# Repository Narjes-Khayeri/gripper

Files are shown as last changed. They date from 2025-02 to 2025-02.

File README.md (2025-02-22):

# two finger robotic gripper
# Abstract
This project focused on designing and building a robotic gripper capable of grasping and holding objects up to 70 grams and 5 cm in diameter. A rack and pinion mechanism with a servo motor was used for gripper movement, and a force sensor (FSR) was calibrated to establish the relationship between force and sensor output. A moving average filter was implemented to reduce sensor fluctuations. Object stiffness was measured, and the required grasping force was estimated using linear regression. A P controller was chosen over PID for simplicity and efficiency. Finally, the gripper successfully held various objects, such as paper cups, eggs, and foosball balls, with appropriate force.

# 3D Model 
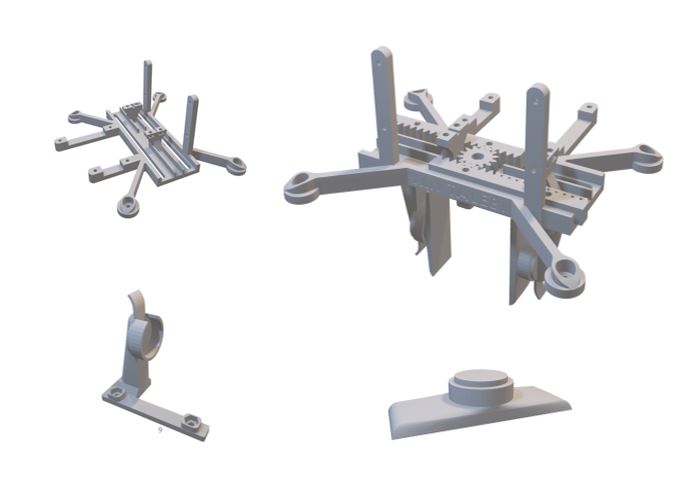
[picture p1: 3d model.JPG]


# FSR Calibration 
In this test, by providing real-world conditions for the sensor and connecting it to the gripper with objects of varying weights, we determined the relationship between the output and the actual value. We also tested this for different series resistances to use the best and most accurate series resistance.
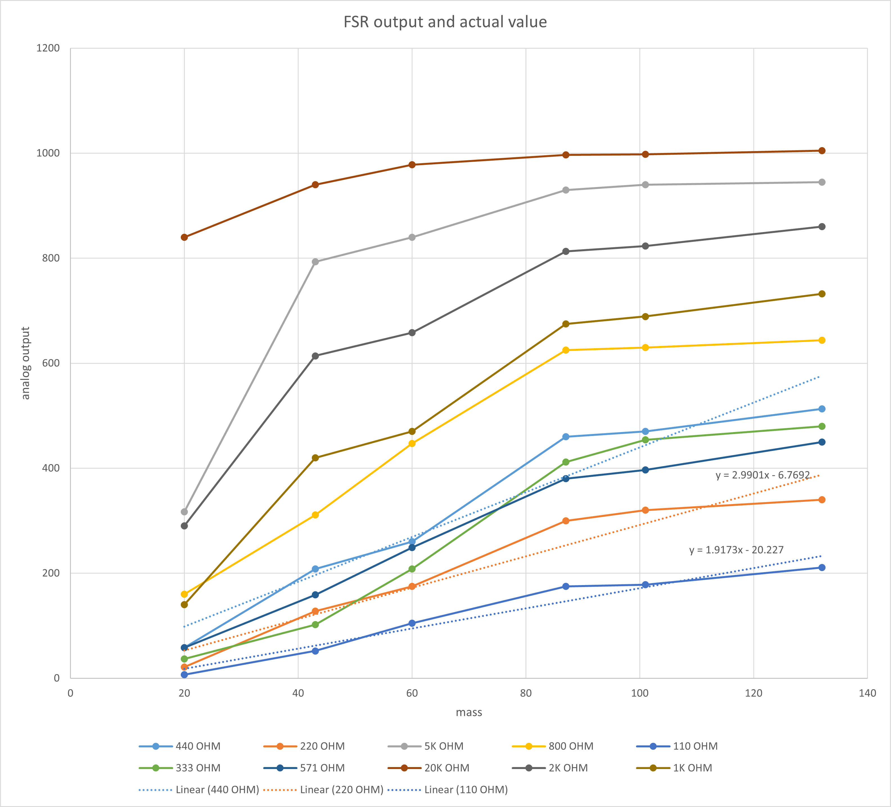
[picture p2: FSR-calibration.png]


 # stiffness detection
 One of the challenges we faced in the project was determining the appropriate force to hold various objects with different masses and stiffnesses. Inspired by an article that assigned specific forces to each stiffness range, we designed a method to obtain the stiffness of objects. By calculating the difference in force and the difference in displacement, the gripper first determines the stiffness coefficient of different objects and then estimates the appropriate force to hold the object.
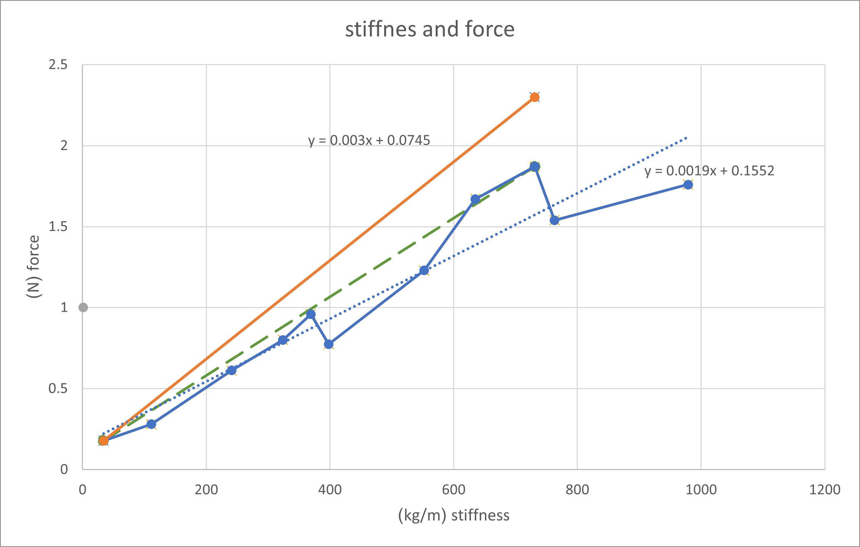
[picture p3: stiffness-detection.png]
 

 # controll method
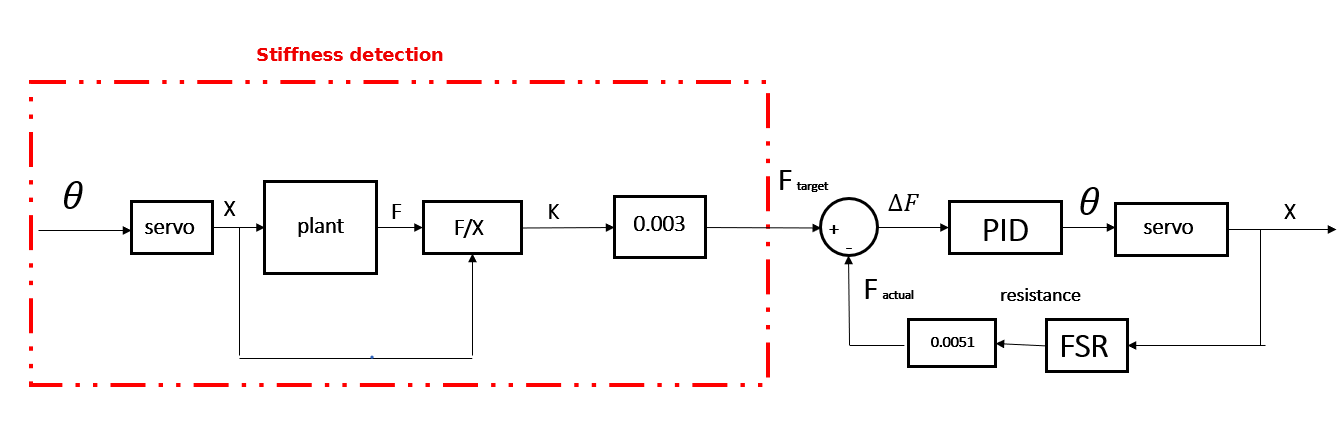
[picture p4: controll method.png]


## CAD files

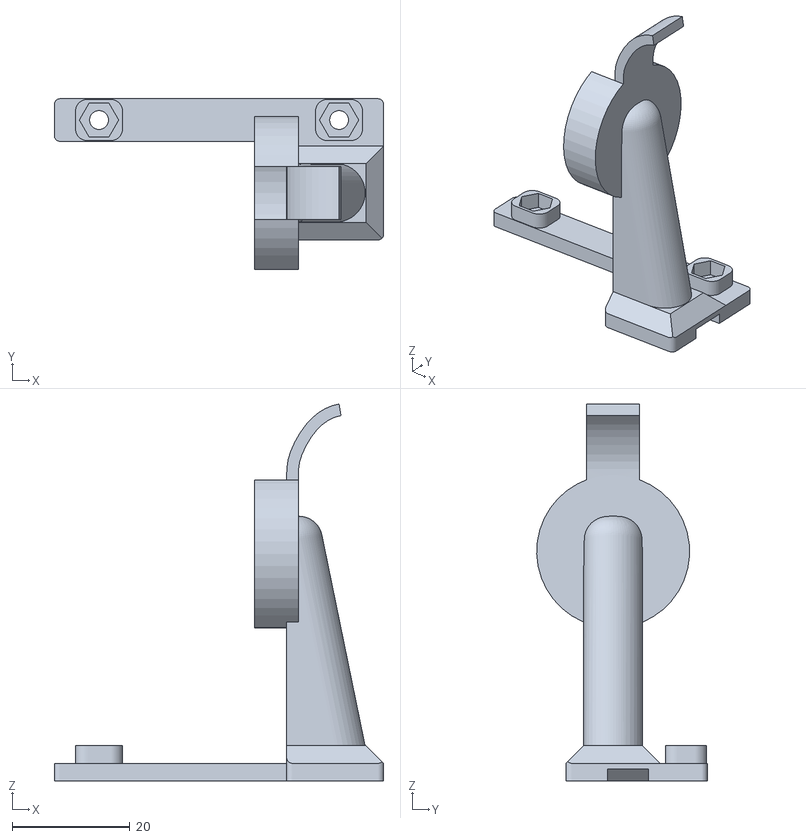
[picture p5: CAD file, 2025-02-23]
3D Model/Jaw_fsr.STL
56.0 x 29.0 x 64.1

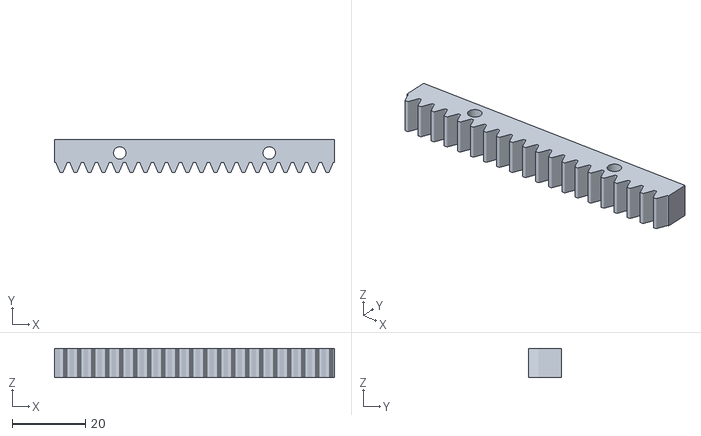
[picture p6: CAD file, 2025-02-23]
3D Model/rack-175-26-14.STL
76.4 x 8.90 x 8.00

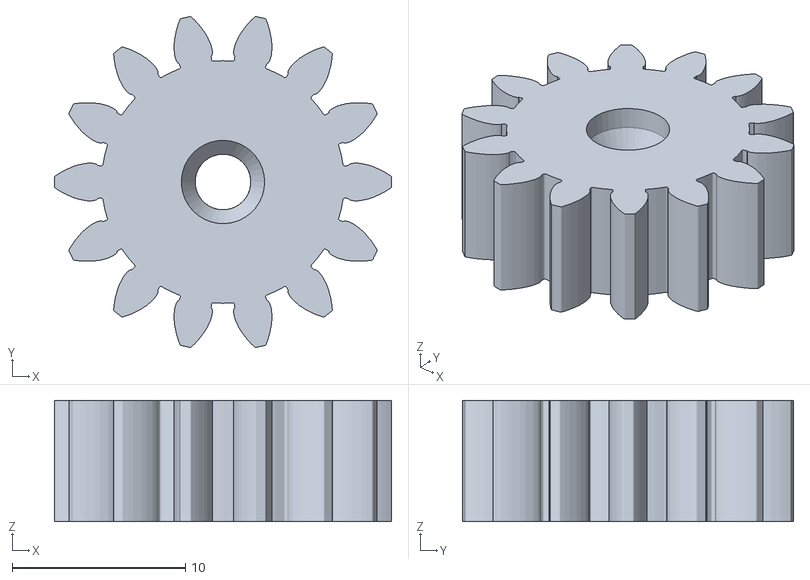
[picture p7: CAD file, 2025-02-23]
3D Model/pinion-175-26-14.STL
19.4 x 19.1 x 7.00

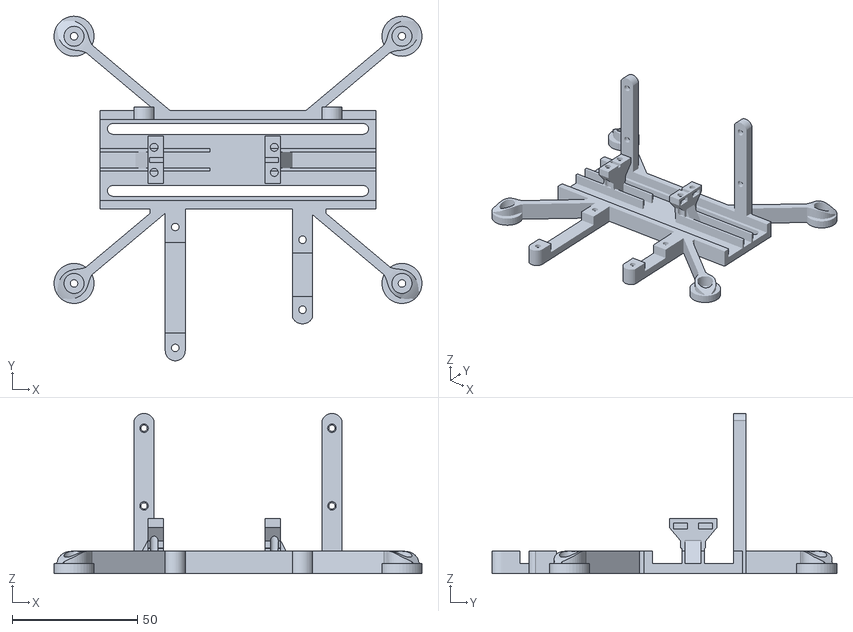
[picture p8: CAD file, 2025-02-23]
3D Model/base.STL
146.9 x 137.5 x 63.9

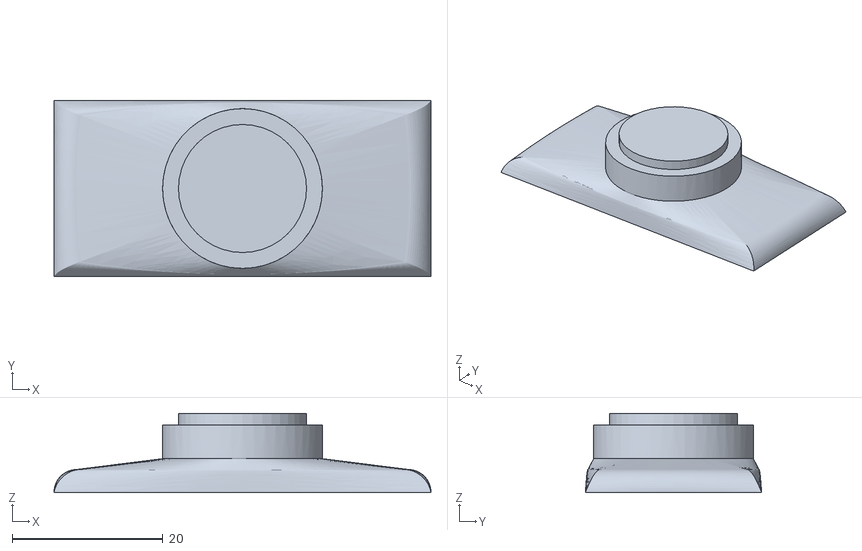
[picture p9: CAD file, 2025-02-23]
3D Model/jaw2.STL
50.0 x 23.4 x 10.5

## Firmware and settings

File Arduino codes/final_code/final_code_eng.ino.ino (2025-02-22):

#include <Servo.h>
#include <LiquidCrystal.h>

// --------------- Pins -----------------
const int buttonPin = 8;  // Button for start
const int servoPin  = 9;  // Servo
const int fsrPin    = A0; // FSR sensor
const int ledPin    = 13; // LED for blinking

// LCD 16x2 in 4-bit mode
// Order: RS, EN, D4, D5, D6, D7
LiquidCrystal lcd(12, 11, 5, 4, 3, 2);

// -------------------- Base Variables --------------------
int   fsrBaseline = 0;       // Baseline after calibration
float fsrFactor   = 0.00511; // Conversion factor from ADC difference to Newton

// Mechanical information
float baseDistance      = 56.0;  // Distance between fingers at 0 degrees
float distancePer175Deg = 52.0;  // Change in distance for 175 degrees

// Servo
Servo myServo;
int servoAngle = 0;

// PID Variables
float Kp = 5.0;
float Ki = 0.0;
float Kd = 0.0;

float integralError = 0.0;
float lastError     = 0.0;
unsigned long lastPIDTime = 0;

// Stiffness and target force
float stiffnessValue   = 0.0;
float initialForce     = 0.0;
float finalForce       = 0.0;
float targetForce      = 0.0;
float lowerBound       = 0.0;
float upperBound       = 0.0;
float finalHoldingForce= 0.0; // Final force that remains within the bounds after PID

// State machine
int state = 0;

/*
   state 0: Waiting for button press
   state 1: Long calibration
   state 2: Stiffness test (holding object until 0.1N + 4 degrees) => only show angle and force while closing
   state 3: Running PID until reaching target force (or timeout) => display "PID in progress..." on LCD
   state 4: Hold for 10 seconds (blink in last 3 seconds) => display stiffness, target force, and final force
   state 5: Open gripper
   state 6: Wait 5 seconds + quick calibration in first 2 seconds + blink in last 3 seconds + return to state=2
*/

// -------------------- Helper Functions --------------------

// Calculate distance between fingers based on servo angle
float getGripperDistance(int angle){
  if(angle > 175) angle = 175;
  return baseDistance - (distancePer175Deg/175.0) * angle;
}

// Read stable FSR (50 samples + remove 4 minimum and 4 maximum)
float getStableForce() {
  const int numSamples = 50;
  int readings[numSamples];

  for(int i=0; i<numSamples; i++){
    readings[i] = analogRead(fsrPin);
    delay(5);
  }

  // Simple sorting
  for(int i=0; i<numSamples-1; i++){
    for(int j=0; j<numSamples-1-i; j++){
      if(readings[j] > readings[j+1]){
        int temp = readings[j];
        readings[j] = readings[j+1];
        readings[j+1] = temp;
      }
    }
  }

  // Remove 4 minimum and 4 maximum values
  long sum = 0;
  int count = 0;
  for(int i=4; i<numSamples-4; i++){
    sum += readings[i];
    count++;
  }

  float avg = sum / (float)count;
  float rawValue = avg - fsrBaseline;
  if(rawValue < 0) rawValue = 0;

  float force = rawValue * fsrFactor;
  return force;
}

// Long calibration
void calibrateFSR() {
  lcd.clear();
  lcd.setCursor(0,0);
  lcd.print("Calibrating...");
  
  const int numReads = 200;
  long sum = 0;
  for(int i = 0; i < numReads; i++){
    sum += analogRead(fsrPin);
    delay(30);
  }
  fsrBaseline = sum / numReads;

  lcd.setCursor(0,1);
  lcd.print("Done Base=");
  lcd.print(fsrBaseline);
  delay(1000);
}

// Quick calibration
void calibrateFSRQuick() {
  lcd.clear();
  lcd.setCursor(0,0);
  lcd.print("Quick Cal...");
  
  const int numReads = 50;
  long sum = 0;
  for(int i=0; i<numReads; i++){
    sum += analogRead(fsrPin);
    delay(20);
  }
  fsrBaseline = sum / numReads;

  lcd.setCursor(0,1);
  lcd.print("Done Base=");
  lcd.print(fsrBaseline);
  delay(800);
}

// Blink LED (3 times, each time 0.5s on + 0.5s off)
void blinkLed3Times(){
  for(int i=0; i<3; i++){
    digitalWrite(ledPin, HIGH);
    delay(500);
    digitalWrite(ledPin, LOW);
    delay(500);
  }
}

// Simple display of "servo angle" and "force" on LCD (two lines)
void displayAngleForce(int angle, float force){
  lcd.clear();
  lcd.setCursor(0,0);
  lcd.print("Angle=");
  if(angle<100) lcd.print("0");
  if(angle<10)  lcd.print("0");
  lcd.print(angle);

  lcd.setCursor(0,1);
  lcd.print("Force=");
  lcd.print(force,2);
}

// Display stiffness, target force, and final force (three parameters)
void displayStiffnessTargetFinal(float stiff, float target, float finalF){
  lcd.clear();
  // Due to limited LCD space, we write it briefly
  // First line: St=? T=?
  lcd.setCursor(0,0);
  lcd.print("St=");
  lcd.print(stiff,2);
  lcd.print(" T=");
  lcd.print(target,2);

  // Second line: F=?
  lcd.setCursor(0,1);
  lcd.print("F=");
  lcd.print(finalF,2);
}

// ----------------------------------------------------------------------
// SETUP
// ----------------------------------------------------------------------
void setup(){
  pinMode(buttonPin, INPUT_PULLUP);
  pinMode(ledPin, OUTPUT);
  digitalWrite(ledPin, LOW);

  lcd.begin(16,2); // LCD 16x2

  myServo.attach(servoPin);
  myServo.write(0);

  // First, enter state 0: Waiting for button press
  state = 0;
}

// ----------------------------------------------------------------------
// LOOP
// ----------------------------------------------------------------------
void loop(){

  switch(state){

    // ------------------------------
    // state 0: Waiting for button press
    // ------------------------------
    case 0:
    {
      // Message on LCD
      lcd.clear();
      lcd.setCursor(0,0);
      lcd.print("Press Button");
      lcd.setCursor(0,1);
      lcd.print("To Start...");

      // Stay here until button is released (HIGH)
      while(digitalRead(buttonPin) == HIGH){
        // Do nothing
      }
      delay(200); // Debounce effect removal
      // When button is pressed:
      state = 1;
    }
    break;

    // ------------------------------
    // state 1: Calibration
    // ------------------------------
    case 1:
    {
      calibrateFSR();
      servoAngle = 0;
      myServo.write(servoAngle);

      // Move to stiffness test
      state = 2;
    }
    break;

    // ------------------------------
    // state 2: Stiffness test (close to 0.1N)
    // ------------------------------
    case 2:
    {
      lcd.clear();
      lcd.setCursor(0,0);
      lcd.print("Meas. Stiffness");

      // 1) Close from angle 0 to 180 until force reaches 0.1N
      for(servoAngle=0; servoAngle<=180; servoAngle++){
        myServo.write(servoAngle);
        float force = getStableForce();

        // As requested: only show angle and force
        displayAngleForce(servoAngle, force);

        if(force >= 0.1){
          initialForce = force;
          break;
        }
      }

      // +4 degrees
      servoAngle += 4;
      if(servoAngle>180) servoAngle=180;
      myServo.write(servoAngle);

      float f2 = getStableForce();
      displayAngleForce(servoAngle, f2);
      finalForce = f2;

      float deltaF = finalForce - initialForce;
      float displacement = 0.001188; // Displacement for 4 degrees
      stiffnessValue = deltaF / displacement;

      delay(800); // Small pause

      state = 3;
    }
    break;

    // ------------------------------
    // state 3: Running PID
    // ------------------------------
    case 3:
    {
      // Simple page for awareness
      lcd.clear();
      lcd.setCursor(0,0);
      lcd.print("PID in progress");

      // Target force = stiffness × 0.0024
      targetForce = stiffnessValue * 0.0024;
      lowerBound  = 0.9 * targetForce;
      upperBound  = 1.1 * targetForce;

      // Prepare PID
      integralError = 0.0;
      lastError = 0.0;
      lastPIDTime = millis();

      // Maximum allowed time
      const unsigned long maxPidTime = 4000; // e.g., 4 seconds
      unsigned long pidStart = millis();

      bool inRange = false;
      finalHoldingForce = 0.0; // Initial zero

      while(true){
        unsigned long now = millis();
        if(now - pidStart > maxPidTime){
          // Time is up
          break;
        }

        float dt = (now - lastPIDTime)/1000.0;
        lastPIDTime = now;

        float force = getStableForce();
        float error = targetForce - force; 

        // PID
        integralError += error * dt;
        float deriv = (error - lastError)/dt;
        lastError = error;

        float output = Kp*error + Ki*integralError + Kd*deriv;

        servoAngle += (int)output;
        if(servoAngle < 0) servoAngle=0;
        if(servoAngle > 180) servoAngle=180;
        myServo.write(servoAngle);

        // If force enters the range, exit
        if(force >= lowerBound && force <= upperBound){
          inRange = true;
          finalHoldingForce = force; // Force when it first entered range
          break;
        }
      }

      if(!inRange){
        // If it failed to enter the range
        finalHoldingForce = getStableForce(); // The value at the end
      }

      state = 4; // Move to holding
    }
    break;

    // ------------------------------
    // state 4: Holding for 10 seconds
    // ------------------------------
    case 4:
    {
      // Throughout the 10s, show stiffness, target force, and final force
      // Write at the beginning and do not change until the end of 10s
      displayStiffnessTargetFinal(stiffnessValue, targetForce, finalHoldingForce);

      unsigned long startTime = millis();
      unsigned long holdDuration = 10000; 
      bool blinkedYet = false;

      while(true){
        unsigned long elapsed = millis() - startTime;
        if(elapsed >= holdDuration) break; // End of 10s

        // Blink in last 3 seconds
        if(elapsed >= 7000 && !blinkedYet){
          blinkLed3Times();
          blinkedYet = true;
        }
        delay(50);
      }

      state = 5;
    }
    break;

    // ------------------------------
    // state 5: Open gripper
    // ------------------------------
    case 5:
    {
      lcd.clear();
      lcd.setCursor(0,0);
      lcd.print("Releasing...");
      servoAngle = 0;
      myServo.write(servoAngle);
      delay(500);

      state = 6;
    }
    break;

    // ------------------------------
    // state 6: 5s wait + quick calibration + blink
    // ------------------------------
    case 6:
    {
      lcd.clear();
      lcd.setCursor(0,0);
      lcd.print("Wait 5s...");
      
      unsigned long startTime = millis();
      bool calDone   = false;
      bool blinkDone = false;

      while(true){
        unsigned long elapsed = millis() - startTime;
        if(elapsed >= 5000) break;

        // First 2s: quick calibration
        if(elapsed < 2000 && !calDone){
          calibrateFSRQuick();
          calDone = true;
        }
        // Last 3s: blink
        if(elapsed >= 2000 && !blinkDone){
          blinkLed3Times();
          blinkDone = true;
        }
        delay(50);
      }

      // End of cycle, go back to state=2 for the next object
      state = 2;
    }
    break;
  } // switch
}

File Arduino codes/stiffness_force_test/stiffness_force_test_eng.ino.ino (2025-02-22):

#include <Servo.h>

const int fsrPin = A0;         // FSR sensor pin
int fsrBaseline = 0;           // Baseline value obtained after calibration
const float fsrFactor = 0.00511; // Conversion factor from ADC difference to Newton (based on experiment)

// Function to store and sort ADC data
// and get the average after removing extreme samples
float getStableForce() {
  const int numSamples = 50;   // Number of samples to take
  int readings[numSamples];

  // Sampling
  for(int i = 0; i < numSamples; i++){
    readings[i] = analogRead(fsrPin);
    delay(5); // Interval between each sample (5ms)
  }

  // Sorting readings using a simple method (bubble sort or any preferred method)
  for(int i = 0; i < numSamples - 1; i++){
    for(int j = 0; j < numSamples - i - 1; j++){
      if(readings[j] > readings[j+1]) {
        int temp = readings[j];
        readings[j] = readings[j+1];
        readings[j+1] = temp;
      }
    }
  }

  // Remove 2 minimum and 2 maximum samples
  // (to reduce the impact of noise and outlier data)
  long sum = 0;
  int count = 0;
  for(int i = 4; i < numSamples - 2; i++){
    sum += readings[i];
    count++;
  }

  // Average of middle samples
  float avgReading = sum / (float)count;

  // Subtract baseline value
  float rawValue = avgReading - fsrBaseline;
  if(rawValue < 0) {
    rawValue = 0;
  }

  // Calculate force (in Newton)
  float force = rawValue * fsrFactor;
  return force;
}

Servo myServo;              // Servo object
int servoAngle = 0;         // Servo angle (0 to 180 degrees)

// Variables for stiffness test
bool stiffnessTestDone = false;   
float initialForce = 0.0;   // Initial force when reaching 0.1N
float finalForce = 0.0;     // Force after an additional 4 degrees of movement
float stiffnessValue = 0.0; // Stiffness value
float deltaForce = 0.0;     // Force difference (finalForce - initialForce)

// =========================
// Sensor calibration function
// =========================
void calibrateFSR(int pin) {
  Serial.println("Calibrating the sensor...");

  // Read the sensor multiple times to get an average and use it as baseline
  const int numReads = 200;
  long sum = 0;
  for (int i = 0; i < numReads; i++) {
    sum += analogRead(pin);
    delay(30);
  }
  fsrBaseline = sum / numReads; // Average value read
  Serial.print("Baseline value is: ");
  Serial.println(fsrBaseline);
  Serial.println("Calibration done. Starting main loop...");
  delay(1000);
}

void setup() {
  Serial.begin(9600);   // Begin serial communication
  myServo.attach(9);    // Attach servo to digital pin 9

  // First, calibrate the sensor
  calibrateFSR(fsrPin);

  // Set the gripper to fully open (zero angle)
  servoAngle = 0;
  myServo.write(servoAngle);
}

void loop() {

  // Until stiffness test is completed:
  if (!stiffnessTestDone) {

    // Move from angle 0 to 180; for each step:
    // 1) Close the servo by 1 degree
    // 2) Read the force using getStableForce() (about ~250ms each time)
    // 3) Print the force
    // 4) If force >= 0.1N, stop
    for (servoAngle = 0; servoAngle <= 180; servoAngle++) {
      myServo.write(servoAngle);

      // Read the stable force using the function above
      float force = getStableForce();

      // Report angle and force with decimal precision
      Serial.print("Angle: ");
      Serial.print(servoAngle);
      Serial.print(" degrees, Force: ");
      Serial.print(force, 3); // Three decimal places
      Serial.println(" Newton");

      // Check if the force threshold is reached
      if (force >= 0.1) {
        initialForce = force; // Initial force at the threshold
        break; // Exit the loop
      }
    }

    // Now close the servo by an additional 4 degrees
    servoAngle += 4;
    if (servoAngle > 180) {
      servoAngle = 180; // Prevent going beyond 180 degrees
    }
    myServo.write(servoAngle);

    // Read the force again
    finalForce = getStableForce();

    // Calculate stiffness
    deltaForce = finalForce - initialForce;
    float displacement = 0.001188; // Meters (displacement between the two fingers at 4 degrees)
    stiffnessValue = deltaForce / displacement;

    // Report stiffness and force difference
    Serial.println("==================================");
    Serial.print("Initial Force (N): ");
    Serial.println(initialForce, 3);
    Serial.print("Final Force (N): ");
    Serial.println(finalForce, 3);
    Serial.print("Force Difference (DeltaF) = ");
    Serial.print(deltaForce, 3);
    Serial.println(" N");
    Serial.print("Object Stiffness (N/m) = ");
    Serial.print(stiffnessValue, 3);
    Serial.println(" N/m");
    Serial.println("==================================");

    // Test completion message
    Serial.println("Stiffness test is complete. Waiting for serial commands (+ or -).");

    // Now the test is finished, and we will enter manual control mode
    stiffnessTestDone = true;
  }
  else {
    // In this phase, the test is complete and we are only waiting for serial commands
    // If '+' is received -> close by one degree
    // If '-' is received -> open by one degree
    // Then read and report the force
    if (Serial.available() > 0) {
      char command = Serial.read();

      if (command == '+') {
        servoAngle++;
        if (servoAngle > 180) {
          servoAngle = 180; // Prevent going beyond 180
        }
        myServo.write(servoAngle);

        // Read and display the force
        float force = getStableForce();
        Serial.print("Angle: ");
        Serial.print(servoAngle);
        Serial.print(" degrees, Force: ");
        Serial.print(force, 3);
        Serial.println(" Newton");
      }
      else if (command == '-') {
        servoAngle--;
        if (servoAngle < 0) {
          servoAngle = 0; // Prevent going below 0
        }
        myServo.write(servoAngle);

        // Read and display the force
        float force = getStableForce();
        Serial.print("Angle: ");
        Serial.print(servoAngle);
        Serial.print(" degrees, Force: ");
        Serial.print(force, 3);
        Serial.println(" Newton");
      }
      // If any other command is received, it will be ignored for now
    }
  }
}

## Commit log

2025-02-22 two finger project
2025-02-22 حذف فایل gripper از ریپازیتوری
